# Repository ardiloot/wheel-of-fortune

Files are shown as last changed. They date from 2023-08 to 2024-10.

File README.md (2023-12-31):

# Wheel of Fortune

## Overview

An over-engineered DIY version of Wheel of Fortune (Wheel or Prizes). The main features are:
* 3 LED strips with individually controllable LEDs (WLED)
* 3 linear servo motors for displaying effect logos
* absolute position optical encoder for wheel position (position depended effects)
* Amplified sound system for theme and effect sound
* ESP32 based LED and servo motor controller
* Orange PI 3 LTS based compute unit
* Node (React + Mantine) app for configuration
* Server stack for metrics, monitoring and backup

Outlook:

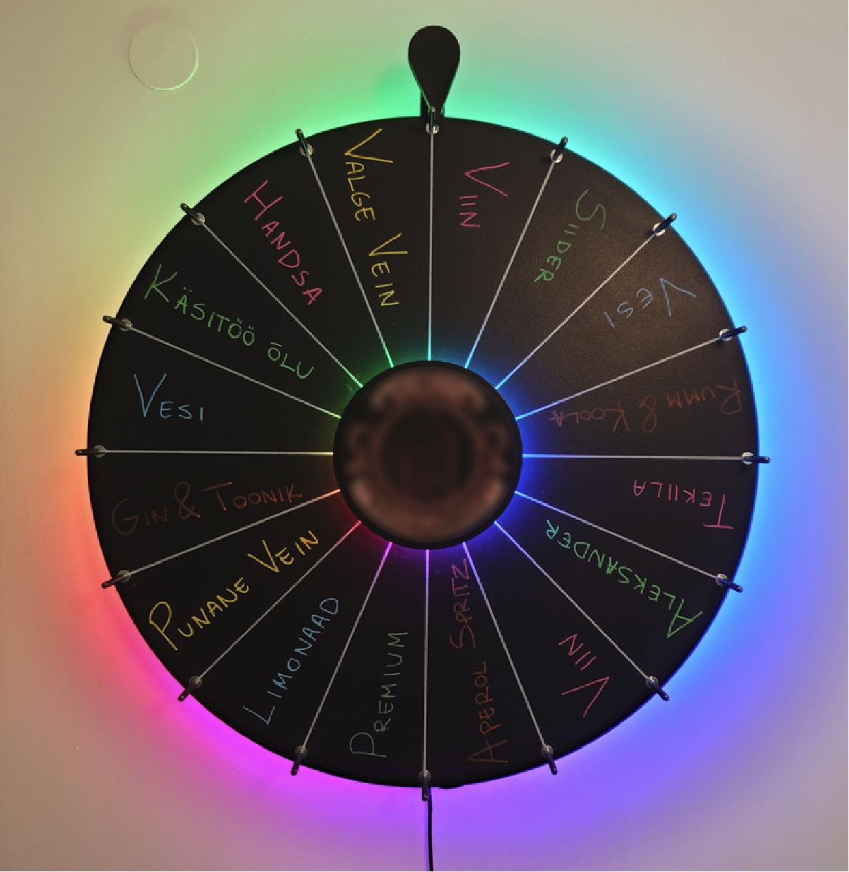
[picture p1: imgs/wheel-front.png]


Internals:

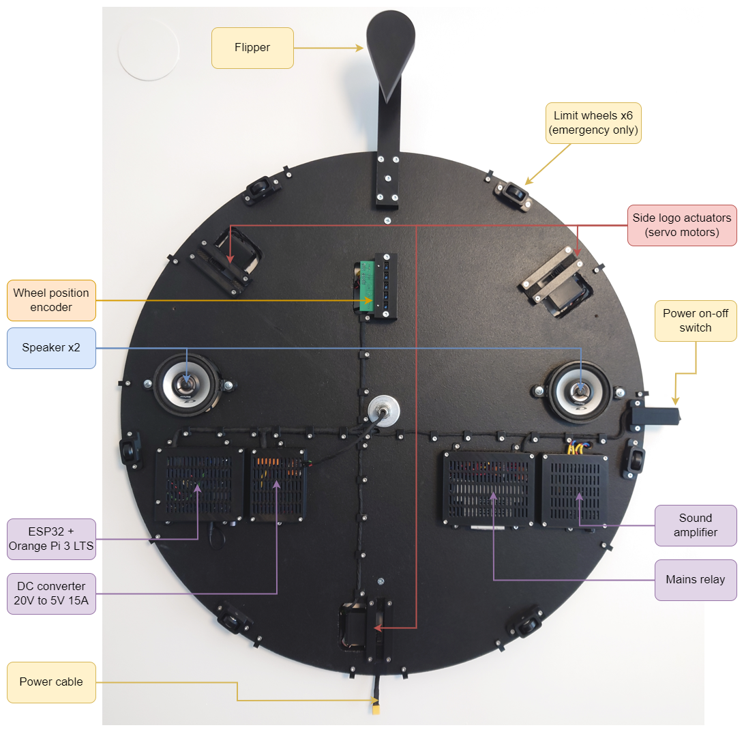
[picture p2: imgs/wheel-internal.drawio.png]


Services:

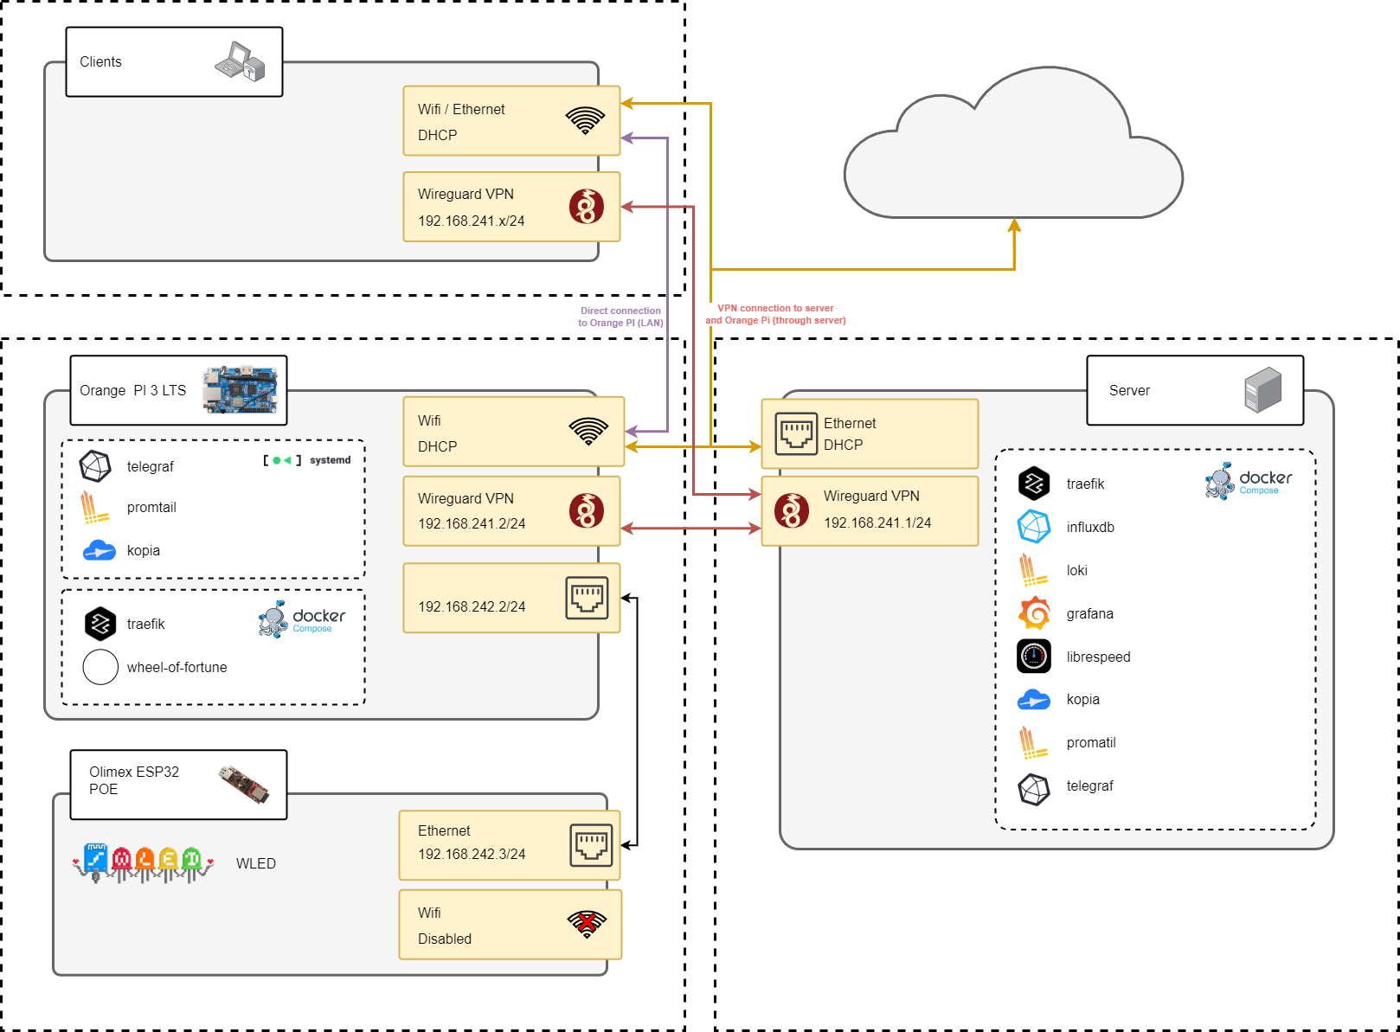
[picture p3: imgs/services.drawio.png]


For detailed instructions how to build the system, see following readme files:

1. [Mechanical setup](hw/mech)
1. [Electrical setup](hw/electrical)
1. [Embedded software](embedded_software)
1. [Server software](server)

## Development

Code is split to two main parts:
1. [Python backend](wheel_of_fortune) (FastAPI)
1. [Node frontend](wheel_of_fortune/frontend) (React + Mantine)

Finally, frontend static HTML + Javascript files are backed into backend Python package and served via backend FastAPI server. 

### Backend

#### Development environment

Python 3.11 is currently preferred, but should also work on any Python >= 3.10

```bash
python -m venv venv
source venv/bin/activate
pip install -r dev-requirements.txt
pip install -e .
```

#### Running backend

```bash
source venv/bin/activate
python -m wheel_of_fortune
```

#### Updating requirements

After adding dependency update requirement files by running:

```bash
source venv/bin/activate
pip-compile --upgrade -o requirements.txt pyproject.toml \
    && pip-compile --extra dev --upgrade -o dev-requirements.txt pyproject.toml \
    && pip-sync dev-requirements.txt
```

### Frontend

#### Setup development environment

Install `nvm` and `node` and install dependencies:

```bash
cd wheel_of_fortune/frontend/
curl -o- https://raw.githubusercontent.com/nvm-sh/nvm/v0.39.4/install.sh | bash
source ~/.bashrc
nvm install
nvm use
npm ci
```

#### Developer mode

Create `.env.local` file for overriding environment:

```bash
VITE_API_URL=https://wheel.int.example.com/api/v1
VITE_WS_URL=wss://wheel.int.example.com/api/v1/ws
```

Run frontend in `dev` mode:

```bash
nvm use
npm run dev
```

#### Release build

```bash
nvm use
npm run build
```

#### Update packages

To update `package-lock.json` and install updates:

```bash
npm update
npm install
```

To also update `package.json` file:

```bash
npm install -g npm-check-updates
ncu -u
npm install
```

### Build steps

Usually not needed, as [Github actions](tree/main/.github/workflows) automatically build and test frontend & docker images. But for completeness, here are commands to do build manually:

#### Frontend

```bash
cd wheel_of_fortune/frontend/
nvm use
npm ci
npm run build
cd ../..
```

#### Backend

```bash
python -m build
```

#### Docker image

```bash
docker build -t wheel_of_fortune .
```

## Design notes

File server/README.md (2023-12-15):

# (Metrics) server setup

## Overview

The aim of this server is to collect logs & telemetry and provide VPN network for Wheel of Fortune:

1.  Server for logs (Loki)
2.  Server for storing telemetry (Influx)
3.  Dashboards for logs and telemetry (Grafana)
4.  VPN network for remote access (WireGuard)
5.  Backup repository (Kopia)

Following services are exposed through Traefik reverse proxy:

- https://traefik.int.example.com - Traefik internal dashboard (basic HTTP auth)
- https://influxdb.int.example.com - Influxdb admin panel
- https://loki.int.example.com - Loki API
- https://grafana.int.example.com - Grafana dashboards
- https://librespeed.int.example.com - Speedtest for testing connection
- https://int.example.com:51515 - Kopia

Throughout this document, `example.com` is use as a example domain name. All services are accessible only over VPN.

## Setup compute instance

One option is to use Oracle Cloud free instance:

- Instance name: wheelmetrics
- Shape: ARM Ampere A1 (VM.Standard.A1.Flex), 1 OCPU, 6 GB RAM
- Image: Canonical Ubuntu 22.04 Minimal aarch64
- Networking: public IPv4 address
- SSH keys: add your public SSH key
- Boot volume: 47 GB

Could use any other cloud provider or local compute.

## Setup domain name

Setup DNS A-type records to point your domain name (`example.com`) to public IP (`a.b.c.d`) of the instance:

```
a.b.c.d     A       example.com
a.b.c.d     A       *.example.com
```

## Setup firewall

Follow steps: https://www.digitalocean.com/community/tutorials/how-to-set-up-a-firewall-with-ufw-on-ubuntu-22-04

## Setup VPN

Follow steps from [Digital Ocean](https://www.digitalocean.com/community/tutorials/how-to-set-up-wireguard-on-ubuntu-22-04) tutorial.

Remember to allow WireGuard port (`51820/udp`) through firewall(s) and allow traffic from developer VPN clients to Wheel of Fortune for remote access:

```bash
sudo ufw allow 51820/udp
sudo ufw route allow in on wg0 out on wg0 to 192.168.241.2
```

As an example, WireGuard could use subnet `192.168.241.0/24`:

1. `192.168.241.1` - current server
2. `192.168.241.2` - Wheel of Fortune (OrangePi)
3. `192.168.241.3` - developer access #1
4. `192.168.241.4` - developer access #2
5. ...

Add DNS records for the server (`int.example.com`) and for Wheel of Fortune VPN ip-address (`wheel.int.example.com`):

```dns
int.example.com             A   192.168.241.1
*.int.example.com           A   192.168.241.1
wheel.int.example.com       A   192.168.241.2
*.wheel.int.example.com     A   192.168.241.2
```

Subdomain `*.int.example.com` correspond to resources accessible over VPN (everything in this case).

## Install docker engine:

Follow steps in: [Installing docker on Ubuntu](https://docs.docker.com/engine/install/ubuntu)

Redirect logging to `journald` for easier scaping by promtail. Create file

```bash
sudo nano /etc/docker/daemon.json
```

with contents

```json
{
   "log-driver": "journald"
}
```

## Setup metrics stack

Clone repository:

```bash
cd ~
git clone https://github.com/ardiloot/wheel-of-fortune.git
```

Copy environment file from the example and fill in values :

```bash
cd ~/wheel-of-fortune/server/metrics
cp env.example .env
nano .env
```

PS: `TELEGRAF_INFLUXDB_*` variables can be filled in later

Start metrics stack:

```bash
docker compose up -d
```

If getting permission errors from Grafana or Loki, run to fix permissions:

```bash
sudo chown 10001:10001  ~/data/loki/
sudo chown 472:472  ~/data/grafana/
```

## Configure influxdb

https://influxdb.int.example.com/

Initial setup:

- Username: admin
- Organization: wheelmetrics
- Bucket name: telegraf

API token for telegraf: (Generate API token -> Custom API token)

- Description: Server's telegraf write token
- Permissions: Add write permissions to telegraf bucket

Create bucket for Wheel of Fortune telemetry: (Buckets -> Create bucket)

- Name: wheel-of-fortune

API token for Wheel of Fortune: (Generate API token -> Custom API token)

- Description: Wheel of Fortune write token
- Permissions: Add write permissions to wheel-of-fortune bucket

Create bucket for Traefik telemetry: (Buckets -> Create bucket)

- Name: traefik

API token for Traefik: (Generate API token -> Custom API token)

- Description: Traefik write token
- Permissions: Add write permissions to traefik bucket

API token for Grafana: (Generate API token -> Custom API token)

- Description: Grafana read all token
- Permissions: Read all buckets

Add generated telegraf token to `.env` file (`TELEGRAF_INFLUXDB_TOKEN`) and restart docker stack `docker compose up -d`.

## Configure Grafana

https://grafana.int.example.com

Default user/password: admin/admin

Add telegraf data source: Administration -> Data sources -> Add data source -> InfluxDB:

- Name: Telegraf
- Query language: InfluxQL
- URL: http://influxdb:8086
- Custom HTTP Headers, select Add Header. Set header to `Authorization` and value to `Token [token]` (previously generated read Token for Grafana)
- Database: telegraf

Add Wheel of Fortune data source: Administration -> Data sources -> Add data source -> InfluxDB:

- Name: Wheel of Fortune
- Query language: InfluxQL
- URL: http://influxdb:8086
- Custom HTTP Headers, select Add Header. Set header to `Authorization` and value to `Token [token]` (previously generated read Token for Grafana)
- Database: wheel-of-fortune

Add Traefik data source: Administration -> Data sources -> Add data source -> InfluxDB:

- Name: Traefik
- Query language: InfluxQL
- URL: http://influxdb:8086
- Custom HTTP Headers, select Add Header. Set header to `Authorization` and value to `Token [token]` (previously generated read Token for Grafana)
- Database: traefik

Add dashboards for Telegraf metrics. For example: https://grafana.com/grafana/dashboards/928-telegraf-system-dashboard/

Add Loki data source: Administration -> Data sources -> Add data source -> Loki:

- Name: Loki
- URL: http://loki:3100

## Configure kopia

For the first start, add `--tls-generate-cert` option to the command to automatically generate TLS certs.

Create repository:

```bash
docker exec -it kopia kopia repository create filesystem --path=/repository
```

Add user for Wheel of Fortune:

```bash
docker exec -it kopia kopia server user add root@wheel-of-fortune
```

Dashboard is located at https://int.example.com:51515

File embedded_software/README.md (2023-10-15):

# Embedded software

## Orange Pi 3 LTS setup

### Burn image to SD card

Follow steps outlined in User Manual (chapters 2.4 - 2.5) to burn Ubuntu server image (`Orangepi3-lts_3.0.8_ubuntu_jammy_server_linux5.16.17.7z`) to SD card.

[Manual and downloads](http://www.orangepi.org/html/hardWare/computerAndMicrocontrollers/service-and-support/Orange-pi-3-LTS.html)

### Initial configuration

Install SD card and power on the Orange Pi board.
To complete initial config, monitor and keyboard must be connected (or Ethernet cable for SSH access). Login using default username & password: orangepi/orangepi

1. Change user password (`passwd`)
2. Connect to WiFi (User Manual chapter 3.8.2)

```bash
nmcli dev wifi
nmcli dev wifi connect [wifi_name] password [wifi_passwd]
```

3. Install updates

```bash
sudo apt-get update
sudo apt-get upgrade
```

4. Add your public SSH key to `~/.ssh/authorized_keys`
5. Disable password login (`sudo nano /etc/ssh/sshd_config`, edit relevant line to `PasswordAuthentication no`)
6. Reboot (`sudo reboot`)

This concludes initial configuration, rest of the configuration can be done over SSH.

### Install WiringOP

Install utilities for controlling GPIO. For more information see User Manual chapter "3.18 How to install wiringOP".

```bash
git clone https://github.com/orangepi-xunlong/wiringOP
cd wiringOP
sudo ./build clean
sudo ./build
```

Test GPIO (should see a table with GPIO current status):

```bash
gpio readall
```

### Set static IP to Ethernet interface

Ethernet port is used to connect to Olimex ESP32 POE running WLED software.
WLED and Ethernet interface should have IP addresses from the same subnet.
In this example, WLED is configured to have static IP `192.168.242.3/24`
and Orange PI's Ethernet port to `192.168.242.2/24`.

```bash
nmcli con mod "Wired connection 1" ipv4.addresses "192.168.242.2/24" ipv4.method "manual"
```

Reboot the system for changes to take effect.

### GPIO permissions

Modify udev rules to allow acces of non-root users to GPIO. Create file

```bash
sudo nano /etc/udev/rules.d/99-gpio.rules
```

with following contents:

```bash
SUBSYSTEM=="gpio", KERNEL=="gpiochip*", ACTION=="add", PROGRAM="/bin/sh -c 'chown root:orangepi /sys/class/gpio/export /sys/class/gpio/unexport ; chmod 220 /sys/class/gpio/export /sys/class/gpio/unexport'"
SUBSYSTEM=="gpio", KERNEL=="gpio*", ACTION=="add", PROGRAM="/bin/sh -c 'chown root:orangepi /sys%p/active_low /sys%p/direction /sys%p/edge /sys%p/value ; chmod 660 /sys%p/active_low /sys%p/direction /sys%p/edge /sys%p/value'"
```

Reboot the system for changes to take effect.

### Install Docker

Install Docker following the instructions from the Docker's home page:
[instructions](https://docs.docker.com/engine/install/ubuntu/#install-using-the-repository).

Also complete [linux postinstall](https://docs.docker.com/engine/install/linux-postinstall/) steps.

By default Docker logs to disk and causes SD card wear.
To avoid that, redirect logging to `journald`. Create file

```bash
sudo nano /etc/docker/daemon.json
```

with contents

```json
{
   "log-driver": "journald"
}
```

## GPIO poweroff service

This service listens GPIO port for shutdown signal (physical poweroff switch).
Only use this service, if poweroff switch is installed. 
For installation, follow instructions from [gpio_poweroff/README.md](gpio_poweroff/README.md).

## Setup VPN (optional)

Follow instructions starting from:
[here] (https://www.digitalocean.com/community/tutorials/how-to-set-up-wireguard-on-ubuntu-22-04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)

Use following configuration:

```bash
sudo nano /etc/wireguard/wg0.conf
```

```
[Interface]
Address = 192.168.241.2
PrivateKey = !REPLACE!

[Peer]
PublicKey = !REPLACE!
Endpoint = example.com:51820
AllowedIPs = 192.168.241.0/24
PersistentKeepalive = 25
```

Configure VPN to always restart:

`sudo systemctl edit wg-quick@wg0.service`

```
[Unit]
StartLimitIntervalSec=0
After=network-online.target
Wants=network-online.target

[Service]
Type=simple
Restart=always
RestartSec=5s
```

## Setup telegraf (optional)

https://docs.influxdata.com/telegraf/v1.21/introduction/getting-started/

1. Install `sudo apt-get install lm-sensors`
1. Enable `outputs.influxdb_v2`
2. Enable `inputs.sensors`

## Setup promtail (optional)

To send logs to Loki, configure promtail to scrape journald.

First, install promtail:

```bash
wget https://github.com/grafana/loki/releases/download/v2.8.4/promtail-linux-arm64.zip
unzip promtail-linux-arm64.zip
rm promtail-linux-arm64.zip
sudo mv promtail-linux-amd64 /usr/local/bin/promtail
# Verify
promtail --version
```

Create configuration file

```bash
sudo mkdir -p /etc/promtail
sudo mkdir -p /var/lib/promtail/
sudo nano /etc/promtail/config.yaml
```

with contents (replace server and auth info).

```yaml
server:
  disable: true

positions:
  filename: /var/lib/promtail/positions.yaml

clients:
  - url: https://[replace]/loki/api/v1/push
    basic_auth:
      username: [replace]
      password: [replace]

scrape_configs:
  - job_name: journal
    journal:
      max_age: 12h
      json: false
      labels:
        job: systemd-journal
    # see https://www.freedesktop.org/software/systemd/man/systemd.journal-fields.html#Trusted%20Journal%20Fields
    # see https://grafana.com/docs/loki/latest/clients/promtail/scraping/#journal-scraping-linux-only
    # NB use `journalctl -n 1 -o json | jq .` to see an actual journal log message (including metadata).
    # NB use `journalctl -n 1 -o json CONTAINER_NAME=date-ticker | jq .` to see a container log message.
    relabel_configs:
      - source_labels: [__journal__hostname]
        target_label: host
      - source_labels: [__journal__systemd_unit]
        target_label: source
      - source_labels: [__journal_container_name]
        target_label: container_name
      - source_labels: [__journal_image_name]
        target_label: image_name
      - source_labels: [__journal_workflow_id]
        target_label: workflow_id
      - source_labels: [__journal__boot_id]
        target_label: boot
      - source_labels: [__journal_priority]
        target_label: priority
    pipeline_stages:
      - template:
          source: priority
          template: '{{ if eq .Value "0" }}{{ Replace .Value "0" "emerg" 1 }}{{ else if eq .Value "1" }}{{ Replace .Value "1" "alert" 1 }}{{ else if eq .Value "2" }}{{ Replace .Value "2" "crit" 1 }}{{ else if eq .Value "3" }}{{ Replace .Value "3" "err" 1 }}{{ else if eq .Value "4" }}{{ Replace .Value "4" "warning" 1 }}{{ else if eq .Value "5" }}{{ Replace .Value "5" "notice" 1 }}{{ else if eq .Value "6" }}{{ Replace .Value "6" "info" 1 }}{{ else if eq .Value "7" }}{{ Replace .Value "7" "debug" 1 }}{{ end }}'
      - labels:
          priority:
```

To start promtail automatically, create a systemd service

```
sudo nano /etc/systemd/system/promtail.service
```

with content:

```
[Unit] 
Description=Promtail service 
After=network-online.target
Wants=network-online.target 

[Service] 
Type=simple 
User=root 
ExecStart=/usr/local/bin/promtail -config.expand-env=true -config.file /etc/promtail/config.yaml 
Restart=on-failure 
RestartSec=20 
 
[Install] 
WantedBy=multi-user.target
```

To enable and test the service, run:

```bash
sudo systemctl daemon-reload
sudo systemctl enable promtail
sudo systemctl start promtail
sudo systemctl status promtail
```

### Setup Kopia (optional)

Install Kopia by following steps from [their webpage](https://kopia.io/docs/installation/#linux-installation-using-apt-debian-ubuntu):

```bash
curl -s https://kopia.io/signing-key | sudo gpg --dearmor -o /etc/apt/keyrings/kopia-keyring.gpg
echo "deb [signed-by=/etc/apt/keyrings/kopia-keyring.gpg] http://packages.kopia.io/apt/ stable main" | sudo tee /etc/apt/sources.list.d/kopia.list
sudo apt update
sudo apt install kopia
```

Setup Kopia to backup to remote repository ([docs](https://kopia.io/docs/repository-server/#on-client-computer)):

```bash
sudo su
kopia repository connect server --url https://int.example.com:51515 --server-cert-fingerprint=[REPLACE]
kopia snapshot create /home/orangepi/data
```

Create service to make daily backups:

`/etc/systemd/system/kopia.service:`

```
[Unit]
Description=Kopia backup
Wants=network-online.target
After=network-online.target

[Service]
Type=oneshot
PrivateTmp=true
Environment="HOME=/root"
ExecStart=/usr/bin/kopia snapshot create --all
```

`/etc/systemd/system/kopia.timer:`

```
[Unit]
Description=Run kopia backup

[Timer]
OnCalendar=daily
Persistent=true
Unit=kopia.service

[Install]
WantedBy=timers.target
```

To enable the service, run:

```bash
sudo systemctl daemon-reload
sudo systemctl enable kopia
sudo systemctl start kopia
sudo systemctl status kopia
```

### Python (optional)

If used for development, install `venv` and `python3-dev`:

```bash
sudo apt-get install python3.10-venv python3-dev
```

## WLED

```bash
git subtree pull --prefix embedded_software/WLED https://github.com/Aircoookie/WLED.git v0.14.0-b4 --squash
```

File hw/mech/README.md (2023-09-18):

# Mechanical design

This file contains documentation for the mechanical design. It is structured as a step-by-step guide to fabricate all necessary components and assemble them together.

NB: Not all details are included in this guide, please consult with the [bill of materials (BOM)](../bom/bom.pdf) and 3D models for complete information.

## 3D printed parts

* Printer: Ender-3 V2 (Trianglelab DDB Extruder V2.0 + BLTouch)
* Slicer: Ultimaker Cura 4.11.0

Rigid parts (PLA+):

* Filamant: eSun PLA+ 1.75mm 1kg Black
* Profile: Standard Quality
* Printing temperature: 210 °C
* Build Plate Temperature: 60 °C
* Initial layer horizontal expansion: -0.1 mm
* Generate support: yes (if needed)

Flexible parts (TPU):

* Filament: Overture TPU Filament, 1.75 mm, black
* Profile: Standard Quality
* Printing temperature: 210 °C
* Build Plate Temperature: 60 °C
* Print speed: 10 mm/s
* Enable retraction: False
* Initial layer horizontal expansion: -0.1 mm

## Wheel assembly

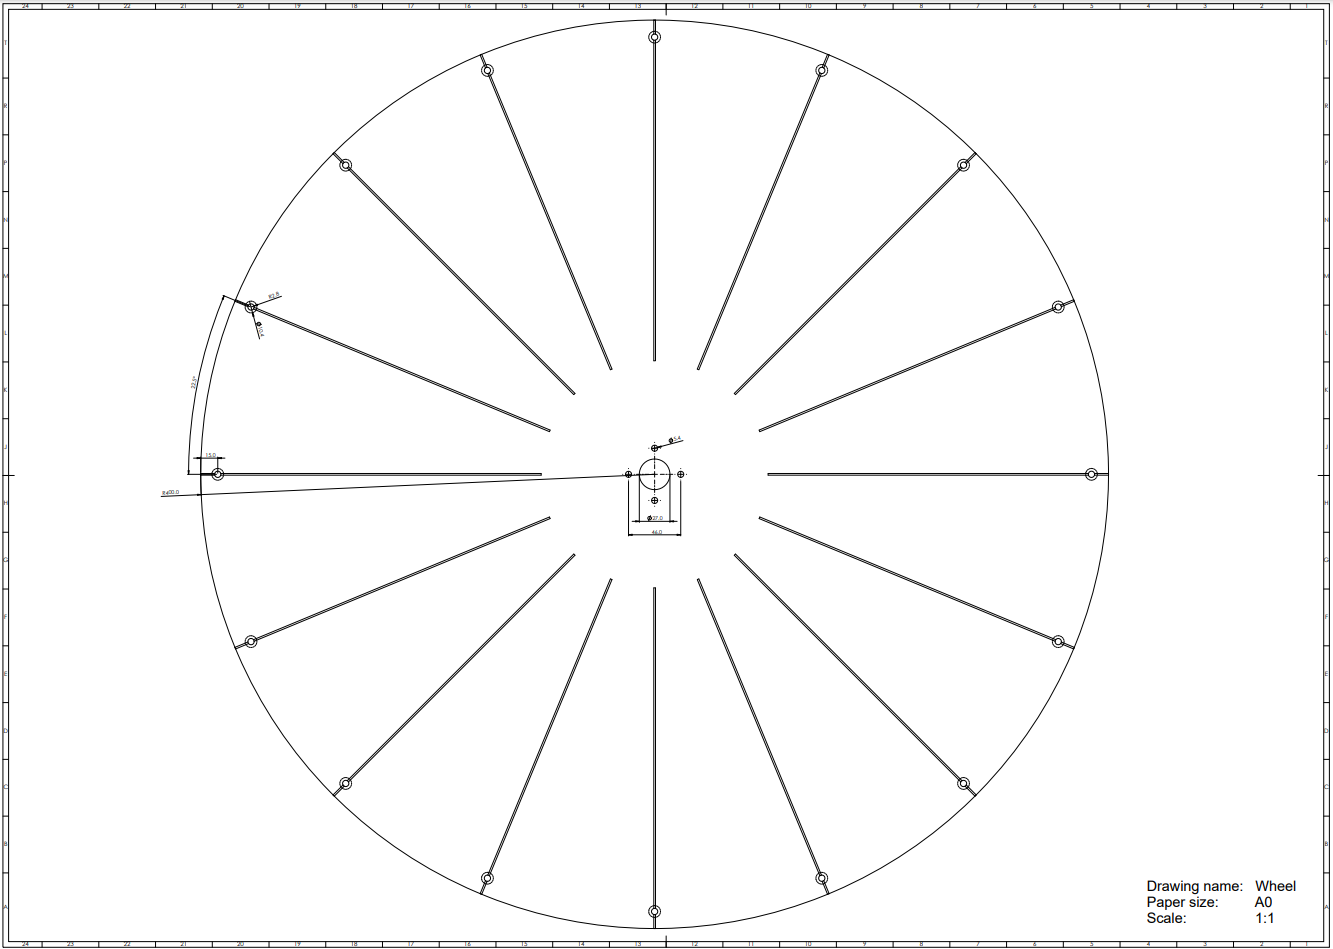
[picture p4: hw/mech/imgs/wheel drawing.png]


[Drawing PDF](wheel/wheel%20drawing.pdf)

[Assembly 3D model](wheel/wheel%20assembly.STL)

### Cut out the wheel

Use drawing to cut out a circle (wheel) from 18 mm thick plywood / particle board. Do not drill any holes yes, before attaching encoder pattern (next step).

### Paint the wheel

Finish the wheel with blackboard paint on the one side and optionally also paint the back side of the wheel (any color). Use appropriate color edge banding to finish the edge.

### Print and glue encoder pattern 

Print [encoder pattern](wheel/encoder_pattern/pattern.pdf) to `A2` sized paper and cut the excess paper outside the pattern (less paper to glue). Use spray glue (or similar) to glue the patter exactly to the center of the wheel.

### Drill holes

Now rest of the holes can be drilled by following the markings on the encoder pattern (center hole, 4 mounting holes and 16 holes for sector separators). To accurately drill the holes for the sector separation rods, it is possible to use following 3D printed [drill aid](wheel/drill%20aid.STL) (needs `605zz 5x14x5mm` bearings or similar, 5 pcs)

### Draw sector separation lines

Use waterproof permanent marker to draw lines between sectors.

### Attach sector separation rods

Attach rods between sectors. Consult [BOM](../bom/bom.pdf) for details.

### Bearing hub

First, print extension to the bearing hub [STL](wheel/bearing%20hub%20ext.STL) as of the shelf bearing hub is not meant to have two bearings inside the hub side-by-side.

Secondly, drill 4 holes into a large washer (`DIN125 M33`) for M5 countersunk heads. Use [drill aid](wheel/drill%20aid%202.STL) (needs `605zz 5x14x5mm` bearings or similar, 4 pcs)

Finally, insert two `SKF6201` (or similar) bearings into the bearing hub and attach them to the wheel by 4 screws (details in [BOM](../bom/bom.pdf)).

### Finishing up

Last step of the wheel assembly is to write names to different sectors to your liking. Liquid chalk markers can be used.

## Backplate assembly

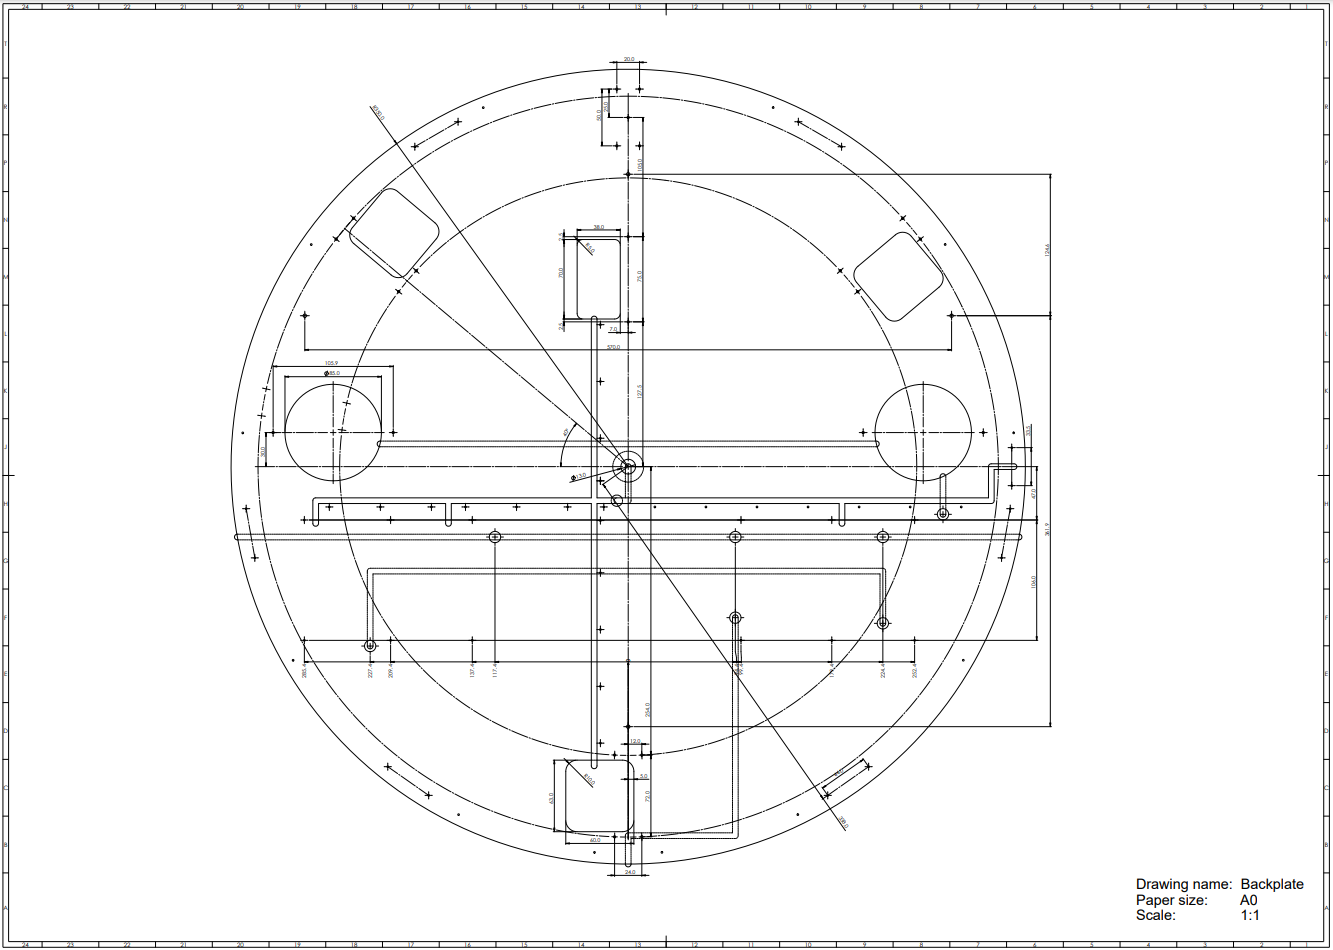
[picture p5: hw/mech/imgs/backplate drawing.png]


[Drawing PDF](backplate/backplate%20drawing.pdf)

[Assembly 3D model](backplate/backplate%20assembly.STL)

### Cut out backplate

Use 18 mm thick plywood / particle board to cut out a circle with 700 mm diameter. As backplate has many holes for mounting sub-assemblies and for passing wires it is advised to print out [drawing](backplate/backplate%20drawing.pdf) to `A0` sized paper and use it as a stencil. This is probably the easiest way to accurately drill/saw all the necessary holes. Also, the stencil can be used in assembly phase to mount all the sub-assemblies correctly.

NB: all/most smaller holes do not need to be drilled, as they are just position markers for wood screws.

### Linear actuator sub-assembly

### Limit wheel sub-assembly

There are 6 limit wheels for stopping the wheel if it is bent by using considerable about of force. In other words, they are only for limiting the movement of the wheel in extreme cases to avoid damaging other components between the wheel and the backplate.

It uses 3D printer pulley wheels and custom 3D printed mount. Consult [BOM](../bom/bom.pdf) for details.

[3D printed parts](backplate/limit%20wheel/limit%20wheel%20assembly.STL)

[Assembly 3D model](backplate/limit%20wheel/limit%20wheel%20assembly.STL)

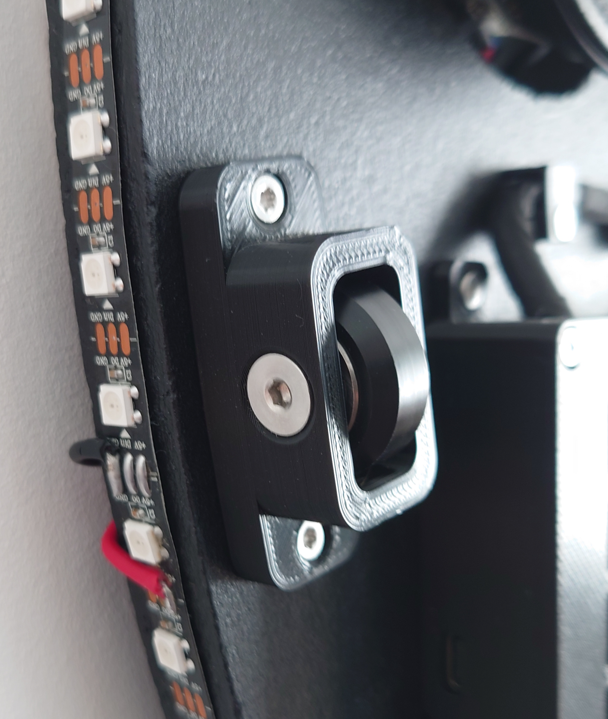
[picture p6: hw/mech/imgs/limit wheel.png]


### Encoder sub-assembly

Encoder sub-assembly if for attaching encoder PCB to the backplate.

[3D printed parts](backplate/encoder)

[Assembly 3D model](backplate/encoder/encoder%20assembly.STL)

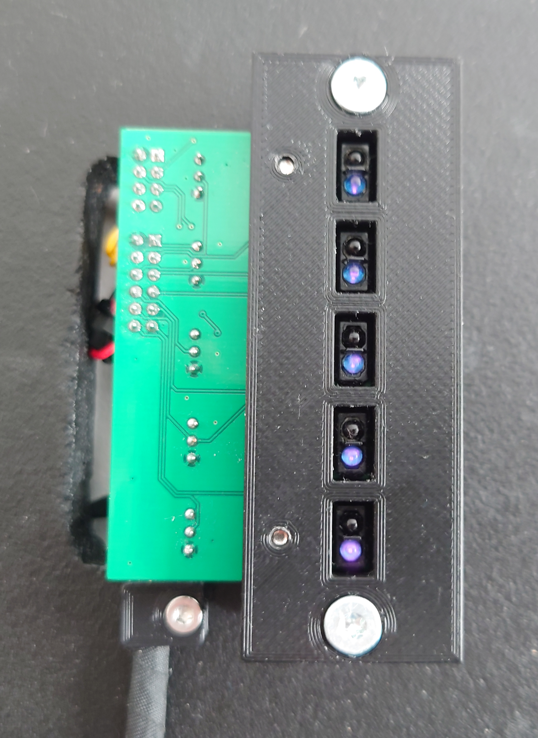
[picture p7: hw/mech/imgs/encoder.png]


### Compute sub-assembly

Compute sub-assembly holds Orange Pi 3 LTS and Olimex ESP32 POE boards. 

[3D printed parts](backplate/compute)

[Assembly 3D model](backplate/compute/compute%20assembly.STL)

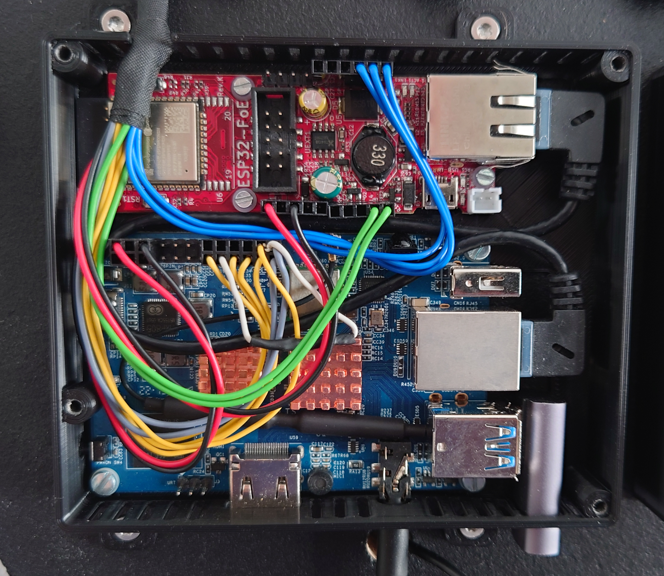
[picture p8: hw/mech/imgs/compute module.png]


### DC converter sub-assembly

DC converter module is for mounting the main DC voltage converter (20 to 5 V). Works as a main power distribution box, as almost everything is powered by 5 V.

[3D printed parts](backplate/dc%20converter)

[Assembly 3D model](backplate/dc%20converter/dc%20converter%20assembly.STL)

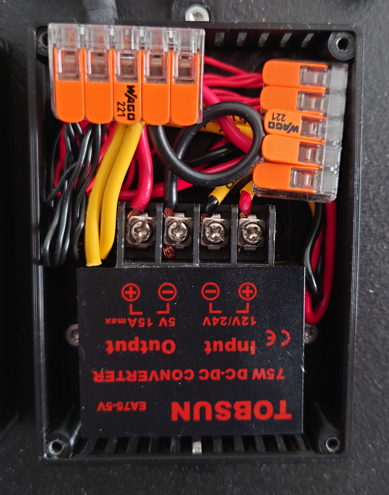
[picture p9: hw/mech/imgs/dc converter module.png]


### Power relay sub-assembly

Power relay module is the main distribution box for 20 V and it also is responsible for switching off the wheel electronics with delay to allow graceful shutdown of the Orange PI board.

[3D printed parts](backplate/power%20relay)

[Assembly 3D model](backplate/power%20relay/power%20relay%20assembly.STL)

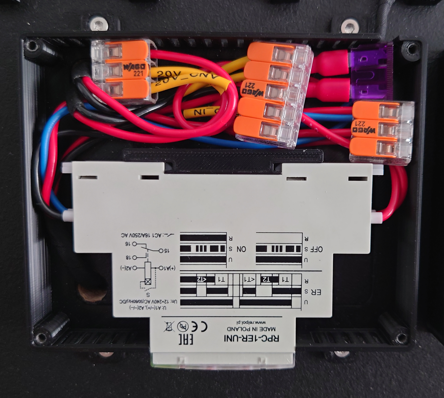
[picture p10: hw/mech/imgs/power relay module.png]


### Amplifier sub-assembly

Mounts sound amplifer and ground loop isolator.

[3D printed parts](backplate/amplifier/)

[Assembly 3D model](backplate/amplifier/amplifier%20assembly.STL)

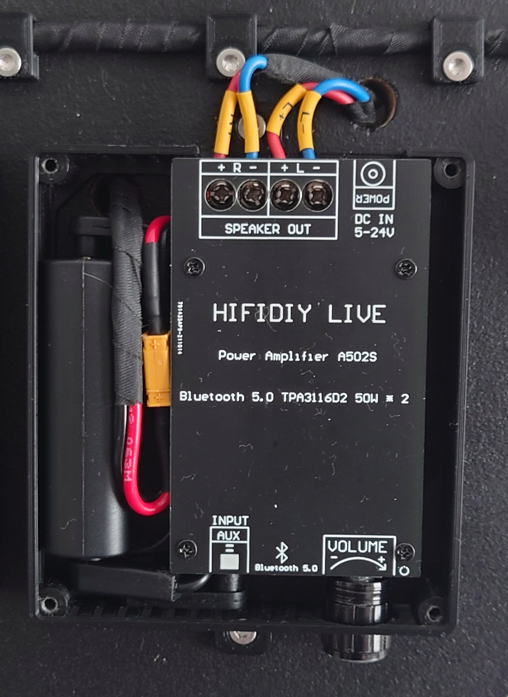
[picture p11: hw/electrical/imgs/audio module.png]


### Flipper sub-assembly

### Power switch sub-assembly

### Speakers

## Cover logo assembly

[Assembly 3D model](cover/cover%20assembly.STL)

## Final assembly

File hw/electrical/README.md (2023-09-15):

# Electrical design

[Wiring diagram](wiring%20diagram.pdf) of the Wheel of Fortune shows how to wire together different modules of the system (displayed as rectangles with round edges). It tries to follow the physical layout of the components if possible. Different wiring colors show different purpose of the wires and are described in the legend. All connectors are displayed from the "top view" (wires going into the screen).

In the following chapters each submodule is separately described together with its connections.

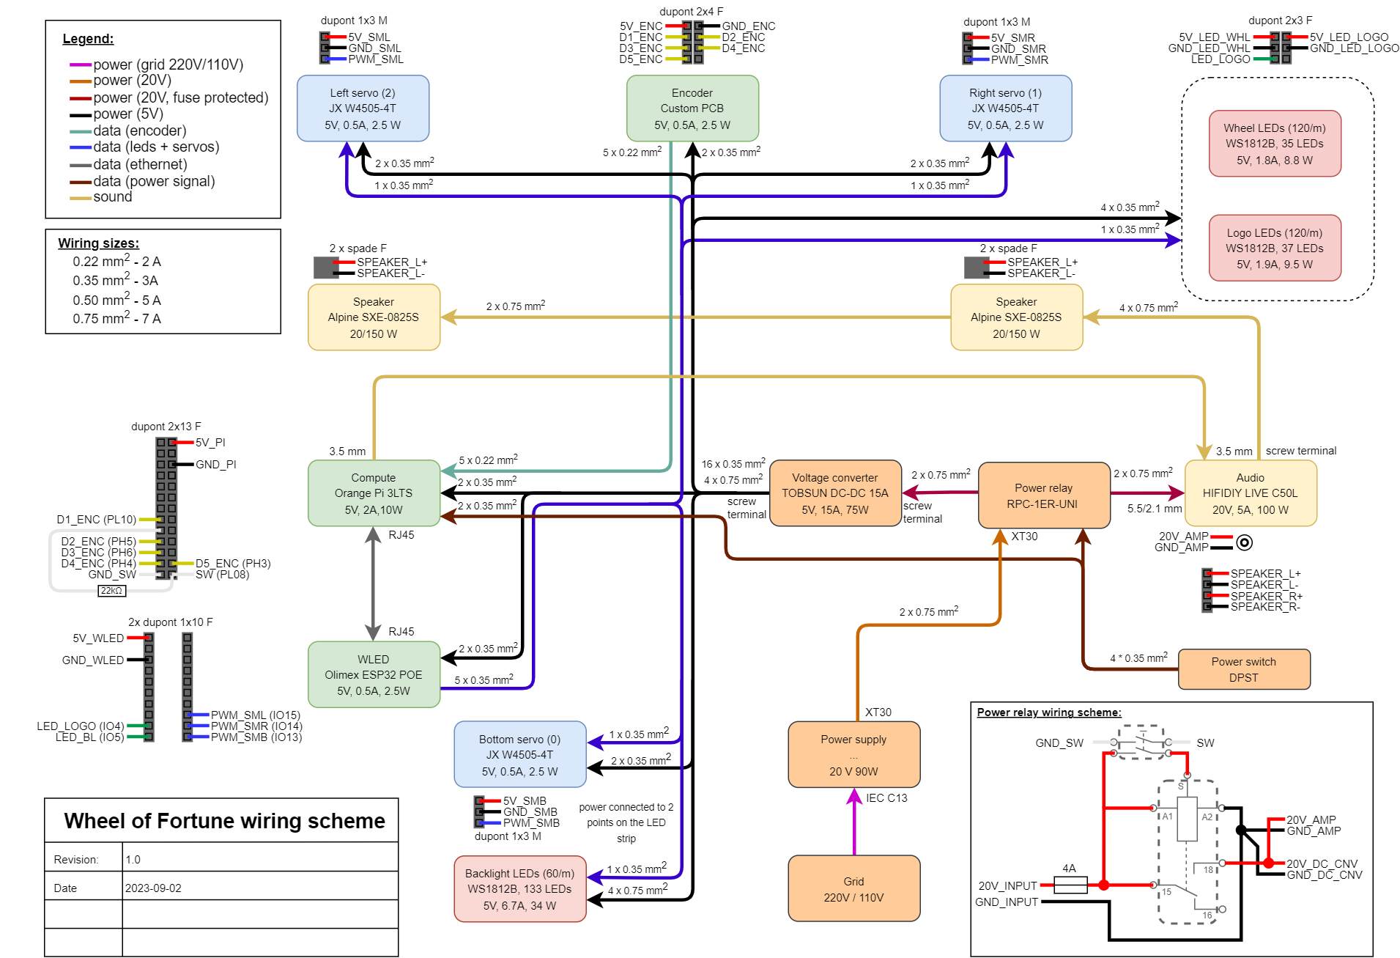
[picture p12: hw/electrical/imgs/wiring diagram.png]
Wiring diagram


## Backlight LEDs

A long led strip attached to the side of the backplate.

As LED strip can draw considerable amount of current (6.7 A), it is advised to power the LED strip form two distinct points (e.g. 1/4 and 3/4). Thick wires should be used (0.75 mm<sup>2</sup>). It is easiest to just solder power wires to the LED strip, but use of connectors is also possible if needed.

Power wires lead to `voltage converter` module and data wire is connected to `WLED` module (ESP32).

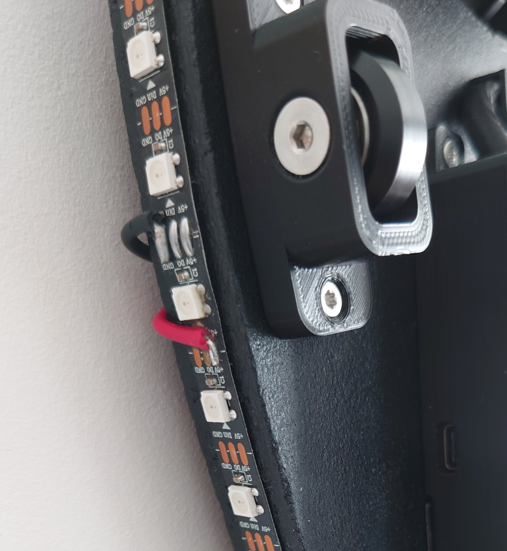
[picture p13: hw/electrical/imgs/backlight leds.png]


## Logo and wheel LEDs

Inside the center logo assembly there are two additional LED strips. Logo LED strip is used as a backlight to the logo and wheel LED strip is illuminating the front of the wheel.

They are powered separately from `voltage converter` module, but they share the data wire (like we have one long LED strip).

## Servo motors

Wheel of Fortune has 3 servo motors (`JX W4505-4T`) used to display side logos. They are regular 5V servos capable of doing multiple turns (to have enough actuation range). They are powered from `voltage converter` module and controlled by `WLED` module (ESP32).

3-pin Dupont connector is used to connect the motor.

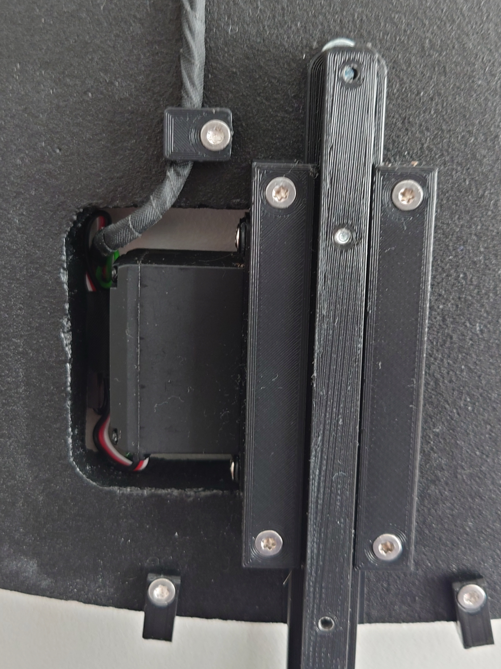
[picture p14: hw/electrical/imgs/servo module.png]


## Encoder

Encoder module contains of 5 line sensors that is used to monitor the encoder pattern attached to the back side of the wheel plate. One sensor is used for clock (and speed) signal and the rest of 4 sensors are used to have absolute positioning of the wheel (2<sup>4</sup> = 16 sectors). Accurate position inside of the sector is not monitored.

Encoder module is powered form `voltage converter` module (5 V) and the position of the wheel is communicated through 5 digital outputs (3.3 V) to `compute` module (Orange Pi).

Details of the schematic and manufacturing of the module can be found in [README](line_sensor_encoder/README.md) file.

Audio module

## Power switch

Power switch is used (`DPST MRS201-3C3`) is used to gracefully power off and on the the electronics. Double Pole Single Throw (DPST) switch is used to send information to the `compute` module (Orange Pi) and to `power relay` module. If power is switched off, the `compute` module can initiate clean shutdown and `power relay` module can start countdown to cut the power (e.g. 30 secs). It should avoid disk corruption of the `compute` module.

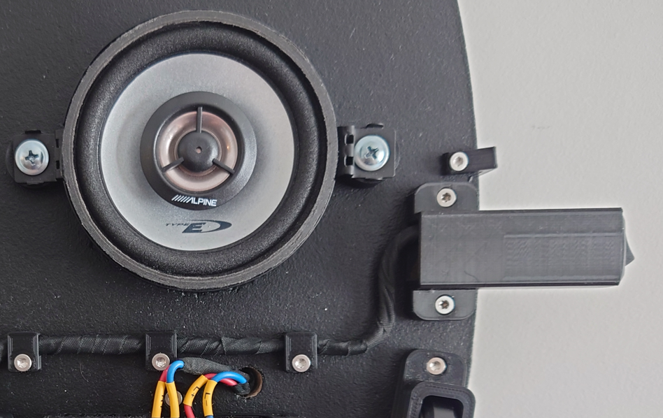
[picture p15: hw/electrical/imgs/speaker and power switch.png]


## Speakers

System has two speakers (`Alpine SXE-0825S`, RMS power 20W, peak power 150W). They are connected with spade connectors to the `audio` module.

## Audio module

Audio module mainly consists of:
1. Audio amplifier (`A502S TPA3116D2 50W`)
2. Ground loop isolator (`Kebidumei`)

Ground loop isolator is needed to avoid noise from the ground loop as Orange Pi (source of audio) and sound amplifier are are sharing ground connection. Adding sound cable is creating a ground loop unless isolator is used.

Module is powered from `power relay` module (20 V). On the image a custom power connector (`XT30`) is used, however standard barrel connector can also be used. Audio signal originates from `compute` module (Orange Pi).



## Compute module

Compute module contains two sub-modules:
1. Orange Pi 3 LTS compute board
2. Olimex ESP32 POE

Orange Pi is the main compute unit of the system. It is powered from 5V and it has encoder module connected to its GPIO pins. Also, it is connected to the power switch to for shutdown signal. Note, that poweroff pin needs pull-up resistor.

ESP32 unit runs modified WLED software and is responsible for controlling LED strips and servo motors. It is powered by 5V and it has 3 PWM outputs for servo motors and 2 outputs for controlling LED strips. For ESP32 pinout see [here](olimex%20esp32%20pinout.pdf).

Two units are connected together with short Ethernet cable.



## Voltage converter

Almost all electronics are running on 5 V and this module is responsible for providing enough 5 V power. As LED strips can be power hungry (full brightness at white color) then this power module must be rated to 15 A (realistic max usage around 12 A).

Here, to keep it simple, a low cost 5 V converter (`TOBSUN 12V/24V TO 5V 15A`) is used together with two `WAGO 221-415` connectors. Module is powered from `power relay` module (20V) and 5 V power is distributed to almost all other module in the system.

NB: Wires from the converter to the WAGO connectors must be rated for 15 A (cross section > 1.5 mm<sup>2</sup>)

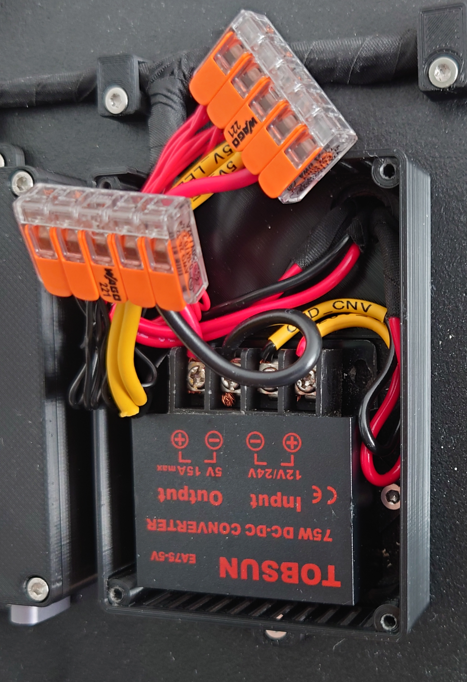
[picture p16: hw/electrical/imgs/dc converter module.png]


## Power relay

The purpose of power relay is to:
1. Delay poweroff (e.g. 30 seconds) to allow graceful shutdown of the `compute` module (Orange Pi)
2. Short protection (fuse)
3. 20 V power distribution box

As this relay will be always powered on (even if the wheel is switched off) a good quality off the shelf timer relay is used (`Relpol RPC-1ER-UNI`) to lower the risk of possible malfunctions. Timer relay is programmed to delay power off by 30 seconds and to delay power on for 2 seconds.

There is a separate wiring diagram for power relay module in the bottom right corner of the diagram. It describes how to connect together timer relay, fuse and power switch. For connections, WAGO connectors are used.

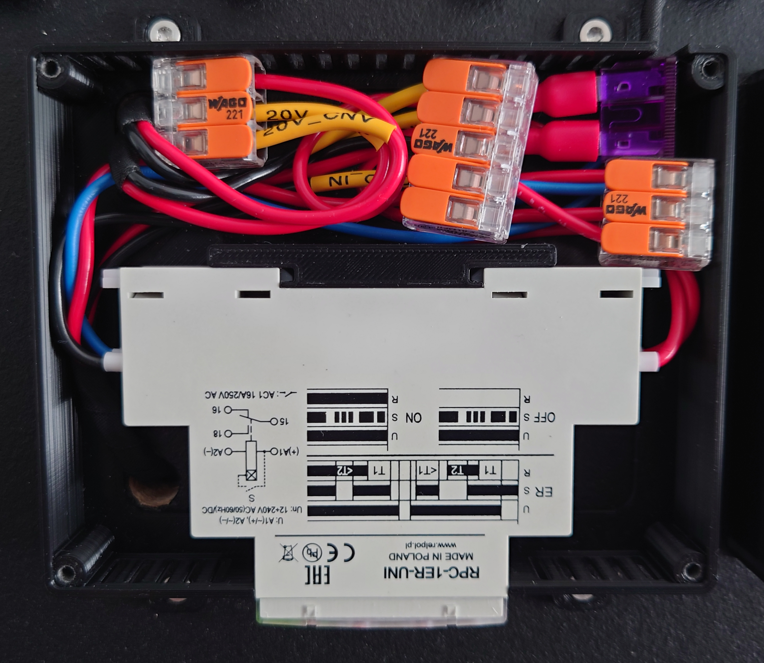
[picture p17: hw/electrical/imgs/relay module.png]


## Power supply

It is recommended to use at least 90 W power supply (19 - 24 V). In this case, `XT30` connector is used for easy replacement of the power supply.

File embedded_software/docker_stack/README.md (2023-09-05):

# Docker Stack for Wheel of Fortune

## Overview

This docker-compose stack provides a convenient way to run the Wheel of Fortune software on embedded computers, such as OrangePi 3 LTS. The stack consists of two containers:
  1. **Wheel of Fortune Container**: This container includes the Wheel of Fortune software.
  2. **Traefik Container**: Traefik is utilized as a reverse proxy to expose the user interface (UI) and the WLED interface. Traefik also provides authentication via Basic HTTP authentication.

## Usage

### Data folder

Copy example data from `wheel-of-fortune/example-data` to `~/data/wheel-of-fortune`. Make necessary changes to the data files.

### Docker stack

Copy/Link `wheel-of-fortune/embedded_software/docker_stack` to `~/docker_stack`.

Add `~/docker_stack/.env` file using following example:

```bash
DOMAIN_NAME=wheel.example.com
INTERNAL_DOMAIN_NAME=wheel.int.example.com
DATA_DIR=/home/orangepi/data

# Variables for Letsencrypt ACME DNS challenge (Cloudflare in this example)
LETSENCRYPT_EMAIL=
CLOUDFLARE_EMAIL=
CLOUDFLARE_DNS_API_TOKEN=

# Wheel of Fortune configuration
WHEEL_NAME=test-wheel
WHEEL_DISPLAY_NAME="Wheel of Fortune"
WHEEL_WLED_URL=
WHEEL_WLED_SEGMENTS='[
    {"name": "ambilight", "start": 0, "stop": 133},
    {"name": "logo", "start": 133, "stop": 170},
    {"name": "wheel", "start": 170, "stop": 205}
]'

# Wheel influxdb metrics
WHEEL_INFLUXDB_URL=https://influxdb.int.example.com
WHEEL_INFLUXDB_TOKEN=
WHEEL_INFLUXDB_ORG=wheelmetrics
WHEEL_INFLUXDB_BUCKET=wheel-of-fortune

# Traefik influxdb metrics
TRAEFIK_INFLUXDB_URL=https://influxdb.int.example.com
TRAEFIK_INFLUXDB_TOKEN=
TRAEFIK_INFLUXDB_ORG=wheelmetrics
TRAEFIK_INFLUXDB_BUCKET=traefik
```

Fill in any missing values and/or make necessary changes to `docker-compose.yml` file.

Add `usersfile` to `config/traefik` folder to list Basic Auth users.
For more information see https://doc.traefik.io/traefik/middlewares/http/basicauth/#usersfile

### Deploy

Start docker stack by

```bash
cd ~/docker_stack
docker compose up -d
```

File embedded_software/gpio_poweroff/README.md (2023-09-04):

# GPIO Poweroff

## Overview

This is a simple service designed to poll a GPIO pin for a poweroff signal. Currently, pin `PL08` (16) is assigned for detecting the shutdown signal. Please ensure that a pull-up resistor is installed.

During regular operation, the pin should remain in a low state. A transition to the high state will trigger the system to initiate a poweroff sequence.

## Installation

Copy Service Files to /opt:

```bash
sudo cp -r ~/wheel-of-fortune/embedded_software/gpio_poweroff /opt/
```

Enable and Start the Service:

```bash
sudo systemctl enable /opt/gpio_poweroff/gpio-poweroff.service
sudo systemctl start gpio-poweroff.service
```

Check Service Status:

```bash
sudo systemctl status gpio-poweroff.service
```

Remember to ensure that the `gpio-poweroff-script.sh` script is properly configured to poll the GPIO pin and trigger the poweroff sequence as needed.

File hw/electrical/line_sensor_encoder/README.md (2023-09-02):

## Line sensor encoder

Back                                        |  Front
:------------------------------------------:|:------------------------------------------:
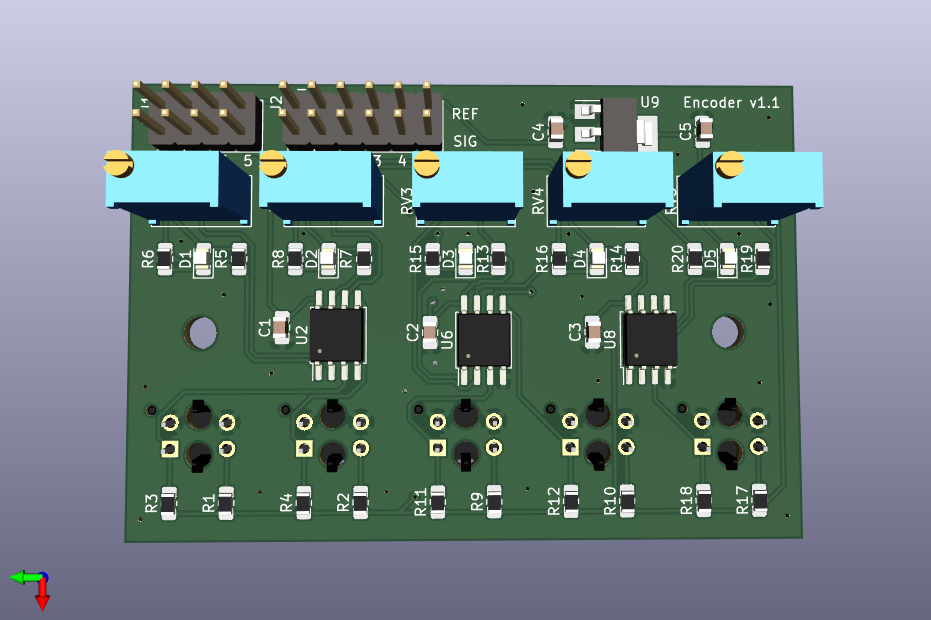
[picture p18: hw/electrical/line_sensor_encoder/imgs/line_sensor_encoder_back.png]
back
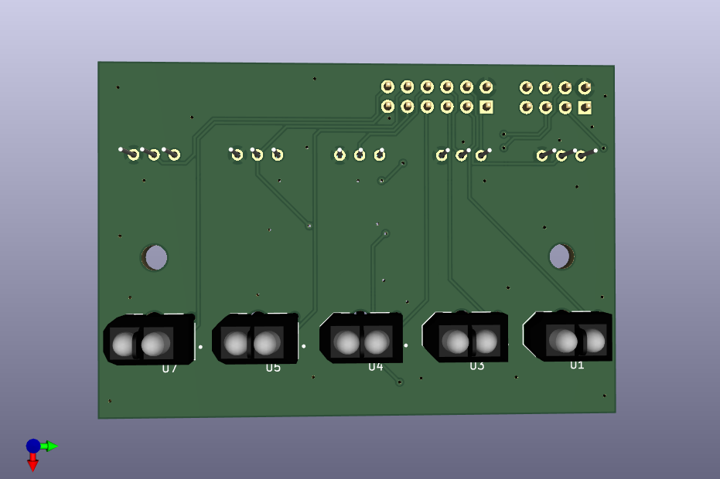
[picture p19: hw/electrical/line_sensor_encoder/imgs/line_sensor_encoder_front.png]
front
  |  

Custom encoder PCB for detecting absolute position of the wheel.
It consists of 5 `TCRT5000L` line sensors combined with voltage comparators
to have five binary outputs.

[PDF schematic](line_sensor_encoder.pdf)

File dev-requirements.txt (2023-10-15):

#
# This file is autogenerated by pip-compile with Python 3.10
# by the following command:
#
#    pip-compile --extra=dev --output-file=dev-requirements.txt pyproject.toml
#
aiocsv==1.2.4
    # via influxdb-client
aiodns==3.1.0
    # via wheel-of-fortune (pyproject.toml)
aiofiles==23.2.1
    # via wheel-of-fortune (pyproject.toml)
aiohttp==3.8.6
    # via
    #   influxdb-client
    #   wheel-of-fortune (pyproject.toml)
aiosignal==1.3.1
    # via aiohttp
annotated-types==0.6.0
    # via pydantic
anyio==3.7.1
    # via
    #   fastapi
    #   starlette
    #   watchfiles
async-timeout==4.0.3
    # via aiohttp
attrs==23.1.0
    # via aiohttp
black==23.9.1
    # via wheel-of-fortune (pyproject.toml)
build==1.0.3
    # via pip-tools
certifi==2023.7.22
    # via influxdb-client
cffi==1.16.0
    # via pycares
charset-normalizer==3.3.0
    # via aiohttp
click==8.1.7
    # via
    #   black
    #   pip-tools
    #   uvicorn
coloredlogs==15.0.1
    # via wheel-of-fortune (pyproject.toml)
exceptiongroup==1.1.3
    # via
    #   anyio
    #   pytest
fastapi==0.103.2
    # via wheel-of-fortune (pyproject.toml)
flake8==6.1.0
    # via wheel-of-fortune (pyproject.toml)
frozenlist==1.4.0
    # via
    #   aiohttp
    #   aiosignal
h11==0.14.0
    # via uvicorn
httptools==0.6.0
    # via uvicorn
humanfriendly==10.0
    # via coloredlogs
idna==3.4
    # via
    #   anyio
    #   yarl
influxdb-client[async]==1.38.0
    # via wheel-of-fortune (pyproject.toml)
iniconfig==2.0.0
    # via pytest
mccabe==0.7.0
    # via flake8
mergedeep==1.3.4
    # via wheel-of-fortune (pyproject.toml)
multidict==6.0.4
    # via
    #   aiohttp
    #   yarl
mypy-extensions==1.0.0
    # via black
opi-gpio==0.5.2
    # via wheel-of-fortune (pyproject.toml)
packaging==23.2
    # via
    #   black
    #   build
    #   pytest
pathspec==0.11.2
    # via black
pip-tools==7.3.0
    # via wheel-of-fortune (pyproject.toml)
platformdirs==3.11.0
    # via black
pluggy==1.3.0
    # via pytest
pycares==4.4.0
    # via aiodns
pycodestyle==2.11.1
    # via flake8
pycparser==2.21
    # via cffi
pydantic==2.4.2
    # via
    #   fastapi
    #   pydantic-settings
pydantic-core==2.10.1
    # via pydantic
pydantic-settings==2.0.3
    # via wheel-of-fortune (pyproject.toml)
pydub==0.25.1
    # via wheel-of-fortune (pyproject.toml)
pyflakes==3.1.0
    # via flake8
pygame==2.5.2
    # via wheel-of-fortune (pyproject.toml)
pyproject-hooks==1.0.0
    # via build
pytest==7.4.2
    # via wheel-of-fortune (pyproject.toml)
python-dateutil==2.8.2
    # via influxdb-client
python-dotenv==1.0.0
    # via
    #   pydantic-settings
    #   uvicorn
    #   wheel-of-fortune (pyproject.toml)
pyyaml==6.0.1
    # via
    #   uvicorn
    #   wheel-of-fortune (pyproject.toml)
reactivex==4.0.4
    # via influxdb-client
six==1.16.0
    # via python-dateutil
sniffio==1.3.0
    # via anyio
starlette==0.27.0
    # via fastapi
tomli==2.0.1
    # via
    #   black
    #   build
    #   pip-tools
    #   pyproject-hooks
    #   pytest
typing-extensions==4.8.0
    # via
    #   black
    #   fastapi
    #   pydantic
    #   pydantic-core
    #   reactivex
    #   uvicorn
urllib3==2.0.6
    # via influxdb-client
uvicorn[standard]==0.23.2
    # via wheel-of-fortune (pyproject.toml)
uvloop==0.18.0
    # via uvicorn
watchfiles==0.21.0
    # via uvicorn
websockets==11.0.3
    # via uvicorn
wheel==0.41.2
    # via pip-tools
yarl==1.9.2
    # via aiohttp

# The following packages are considered to be unsafe in a requirements file:
# pip
# setuptools

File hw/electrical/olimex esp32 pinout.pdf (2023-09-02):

pin | name | comment | connected to
1 | 5V | | 5V
2 | 3.3V
3 | GND | | GND
4 | ESP_EN | reset
5 | GPIO0 | boot pin
6 | GPIO1 | UART
7 | GPIO2 | 2.2k pullup
8 | GPIO3 | UART
9 | GPIO4 | OK | LED1
10 | GPIO5 | 10k pullup | LED2
1 | GPI39 | input only, ext power sense
2 | GPI36 | input only, 10k pullup | ENC1
3 | GPI35 | input only, opt battery | ENC2
4 | GPI34 | input only, button, 10k pullup
5 | GPIO33 | ok | ENC3
6 | GPIO32 | ok | ENC4
7 | GPIO16 | 2.2k pullup | ENC5
8 | GPIO15 | 10k pullup | SERVO1
9 | GPIO14 | OK | SERVO2
10 | GPIO13 | 2.2k pullup | SERVO3

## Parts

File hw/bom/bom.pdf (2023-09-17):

sub-assembly | type | name | quantity | url
audio | 3D printed part | amplifier mount | 1
audio | 3D printed part | amplifier cover | 1
audio | screw | DIN912 M3x6 | 4
audio | screw | wood screw 3x20 torx | 2
audio | device | amplifier A502S TPA3116D2 50W | | 1 https://vi.aliexpress.com/item/1005003447250822.html
audio | device | kebidumei ground loop isolator | | 1 https://vi.aliexpress.com/item/1005001604545947.html
audio | cable | audio cable flat 20cm | | 1 https://vi.aliexpress.com/item/10000360130480.html
compute | 3D printed part | compute mount | 1
compute | 3D printed part | compute cover | 1
compute | screw | DIN912 M3x6 | 4
compute | screw | wood screw 3x20 torx | 4
compute | device | Orange PI 3 LTS | | 1 http://www.orangepi.org/html/hardWare/computerAndMicrocontrollers/detail
compute | device | Olimex ESP32 POE | | 1 https://www.olimex.com/Products/IoT/ESP32/ESP32-POE/open-source-
compute | screw | D84 M3x5 | 4
compute | screw | D84 M2x5 | 3
compute | washer | nylon M3 | 4
compute | washer | nylon M2 | 3
compute | cable | usb bend UC-095F | | 1 https://vi.aliexpress.com/item/1005005200683069.html
compute | cable | ethernet cable Left-Right, 25cm | | 1 https://vi.aliexpress.com/item/1005002782553550.html
dc-converter | 3D printed part | dc converter mount
dc-converter | 3D printed part | dc converter cover
dc-converter | dc-converter | TOBSUN 12V 24V TO 5V 15A | | 1 https://vi.aliexpress.com/item/4001107349411.html
dc-converter | connector | WAGO 221-415 | 2
dc-converter | screw | DIN912 M3x6 | 4
dc-converter | screw | wood screw 3x20 torx | 4
encoder | 3D printed part | encoder mount | 1
encoder | screw | wood screw 4x40 torx | 2
encoder | sensor | line sensor TCRT5000L | 5
encoder | pcb | JLCPCB manufacturing (5 pcb) | 1
encoder | potentiometer | 3296W 10k | 5
encoder | comparator | LM393ADT | 5
encoder | screw | DIN912 M3x5 | 2

encoder | washer | nylon washer M3 | 2
flipper | 3D printed part | flipper mount | 1
flipper | 3D printed part | flipper fixed spring cover | 1
flipper | 3D printed part | flipper damper | 1
flipper | 3D printed part | flipper inset | 1
flipper | 3D printed part | flipper bumper | 1
flipper | screw | ISO10642 M4x10 | 4
flipper | screw | ISO7380 M4x12 | 2
flipper | washer | DIN125 M4 | 1
flipper | standoff | Wurth 970700471 M4x70 | 1 https://ee.farnell.com/wurth-elektronik/970700471/abstandhalt-6kant-innen-
flipper | bearing hub | MT164-624ZZ-10-4 | 1 https://vi.aliexpress.com/item/33010273520.html
flipper rubber band | | 1
flipper damper | leather | 1
flipper | spring | 10x42x0.9 mm | 1
flipper | screw | wood screw torx 4x40 | 5
limit wheel | 3D printed part | limit wheel mount | 6
limit wheel | washer | DIN125 M5 | 12
limit wheel | screw | ISO10642 M5x20 | 6
limit wheel | wheel | 3D printed part printer wheels 625ZZ | 6 https://vi.aliexpress.com/item/1005003786298839.html
limit wheel | screw | wood screw 3x20 torx | 12
power relay | 3D printed part | relay mount | 1
power relay | 3D printed part | relay mount cover | 1
power relay | screw | DIN912 M3x6 | 4
power relay | screw | wood screw 3x20 torx | 4
power relay | time relay | Relpol RPC-1ER-UNI | 1 https://www.sakt.ee/en/time-relays/8872-rpc-1er-uni-time-relay-12-240acdc-
power relay | fuse | 4A car fuse | 1
power relay | connector | WAGO 221-413 | 2
power relay | connector | WAGO 221-415 | 1
power switch | 3D printed part | power switch mount | 1
power switch | switch | DPST MRS201-3C3 | 1 https://www.oomipood.ee/product/mrs201_3c3_klahvluliti_2_on_off_3a_250v
power switch | screw | wood screw torx 3x25 | 2
linear actuator | 3D printed part | gear | 3
linear actuator | 3D printed part | logo mount | 3

linear actuator | 3D printed part | railings | 3
linear actuator | 3D printed part | gear rack | 3
linear actuator | 3D printed part | demo logo | 4
linear actuator | servo | JX W4505-4T | 3
linear actuator | screw | wood screw torx 3x25 | 12
speaker | 3D printed part | speaker stud 1 | 2
speaker | 3D printed part | speaker stud 2 | 2
speaker | screws | flat head wood screw 4x25 | 4
speaker | speaker | Alpine SXE-0825S | 2 https://www.alpine.co.uk/p/Products/SingleView/SXE-0825S
backplate | wood | particle board / plywood 18 mm | 1
backplate | screw | ISO10642 M12x70 full thread | 1 https://vi.aliexpress.com/item/1005004860869917.html
backplate | washer | DIN440 M12 | 1
backplate | nut | DIN439 M12 | 1
backplate | 3D printed part | wire clip small | 57
backplate | 3D printed part | wire clip large | 3
backplate | 3D printed part | led strip clip | 12
backplate | screw | wood screw 3x20 torx | 72
backplate | led strip | WS2812, 3m back, 60 leds/m | 1
cover | 3D printed part | cover logo | 1
cover | 3D printed part | cover base | 1
cover | 3D printed part | cover led ring | 1
cover | 3D printed part | cover locker | 1
cover | 3D printed part | cover logo backlight | 1
cover | 3D printed part | cover mantle | 1
cover | led strip | 5mm Black WS2812, 1m, 120 leds/m | 1
cover | led strip | WS2812, 1m back, 60 leds/m | 1
cover | screw | ISO10642 M3x10 | 8
cover | screw | ISO10642 M3x16 | 8
cover | screw | DIN914 45H M3x6 | 3
wheel | 3D printed part | bearing hub ext | 1
wheel | washer | DIN7349 (5,3X15X2,0) | 16
wheel | screw | ISO10642 M5X30 | 16
wheel | pins | DIN7979 M5 8x60 | 16

wheel | washer | DIN125 M33 | 1
wheel | screw | ISO10642 M5X45 | 4
wheel | washer | DIN433 M12 | 1
wheel | washer | DIN125 M12 | 1
wheel | nut | DIN934 M12 | 1
wheel | bearing | SKF6201 | 2 https://www.stokker.ee/kuullaager-6201-2z-skf-c-6201%7C2z-skf
wheel | bearing hub | MT164-6201ZZ-15-12 | 1 https://vi.aliexpress.com/item/33010273520.html
wheel | wood | particle board / plywood 18 mm | 1
wheel | bearing | 605zz 5x14x5mm | 8 https://vi.aliexpress.com/item/1005003477513135.html
wiring | wire | 0.75 red H05VK075RT | 6
wiring | wire | 0.75 black H05VK075SW | 6
wiring | wire | 0.35 red FLRY-B0.35-BK | 8
wiring | wire | 0.35 red FLRY-B0.35-RD | 8
wiring | wire | 0.35 gray FLRY-B0.35-GY | 4
wiring | wire | 0.35 gray FLRY-B0.35-GR | 4
wiring | wire | 0.22 yellow FLRY-A0.22-YL | 4
wiring | connector | XT30U-F | 2
wiring | connector | XT30U-M | 2 https://www.oomipood.ee/product/67783_gby_3_5mm_stereo_otse_pistik_3
wiring | cable | audio cable 1m | 1
finish | permanent marker | white 2mm | 1 https://www.k-rauta.ee/p/veekindel-marker-2-mm-valge/e8xu
finish | blackboard paint | Tikkurila 0.3L | 1 https://www.k-rauta.ee/p/eriotstarbeline-varv-tikkurila/aju
finish | chalk markers | Liquid chalk Apli | 1 https://vunder.ee/en/product/liquid-chalk-apli/
power supply | power supply | 20V 90W | 1
power supply | extension coord | 3m XT30 | 1

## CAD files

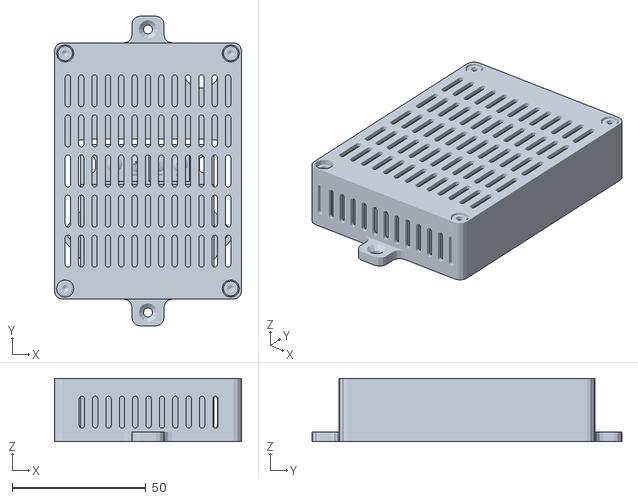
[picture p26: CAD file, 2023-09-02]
hw/mech/backplate/dc converter/dc converter assembly.STL
70.0 x 116.0 x 23.6

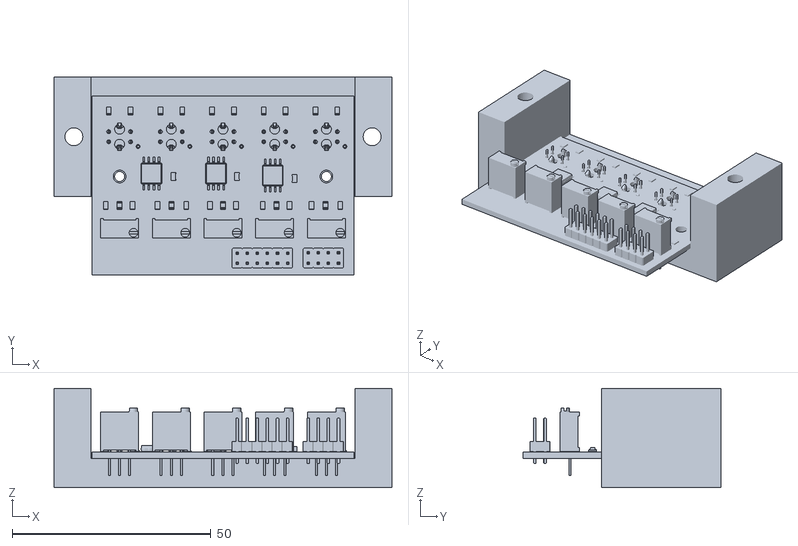
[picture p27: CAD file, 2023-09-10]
hw/mech/backplate/encoder/encoder assembly.STL
85.0 x 49.8 x 25.0

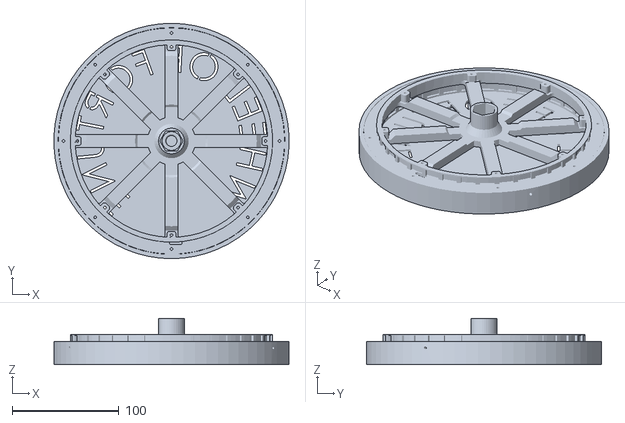
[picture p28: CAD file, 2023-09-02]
hw/mech/cover/cover assembly.STL
219.7 x 220.0 x 43.1

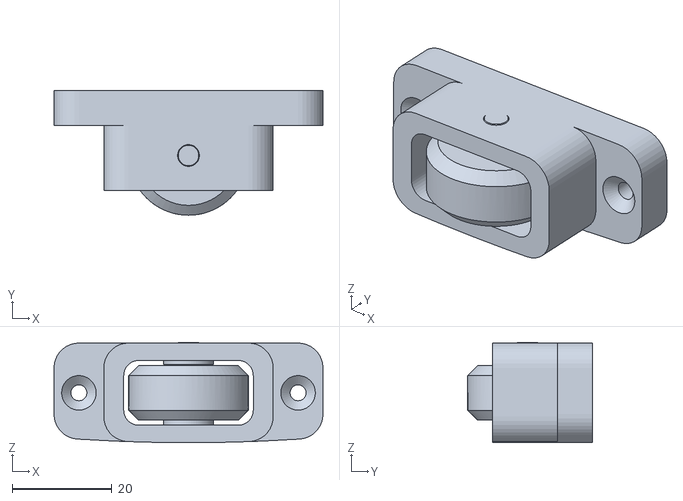
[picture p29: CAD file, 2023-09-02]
hw/mech/backplate/limit wheel/limit wheel assembly.STL
54.0 x 25.0 x 20.1

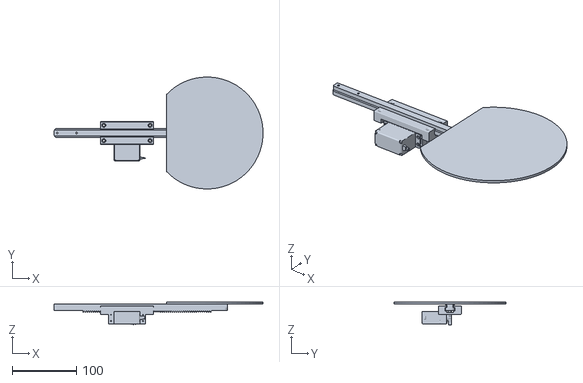
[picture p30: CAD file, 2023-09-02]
hw/mech/backplate/linear actuator/linear actuator assembly.STL
324.9 x 173.9 x 35.1

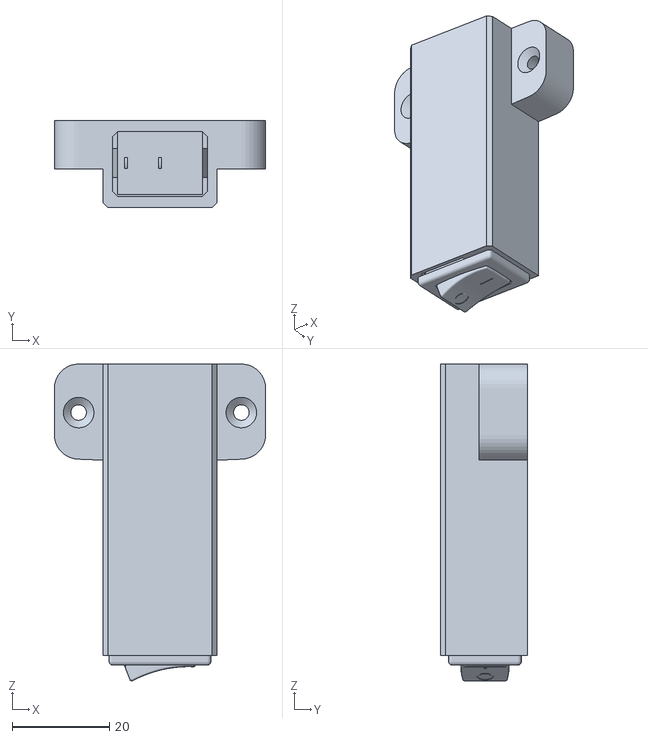
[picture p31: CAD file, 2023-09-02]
hw/mech/backplate/power switch/power switch assembly.STL
43.5 x 17.9 x 65.3

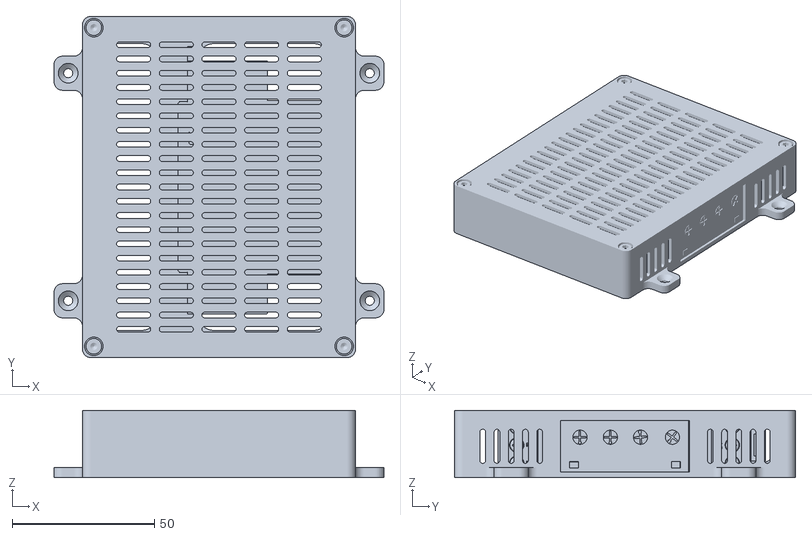
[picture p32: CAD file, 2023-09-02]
hw/mech/backplate/power relay/power relay assembly.STL
116.0 x 120.0 x 23.6

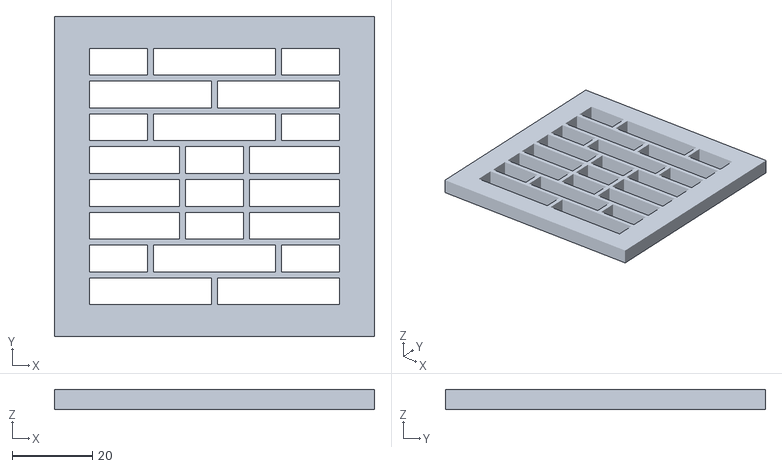
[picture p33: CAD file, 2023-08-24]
embedded_software/WLED/usermods/word-clock-matrix/Word Clock Baffle.stl
80.0 x 80.0 x 5.00

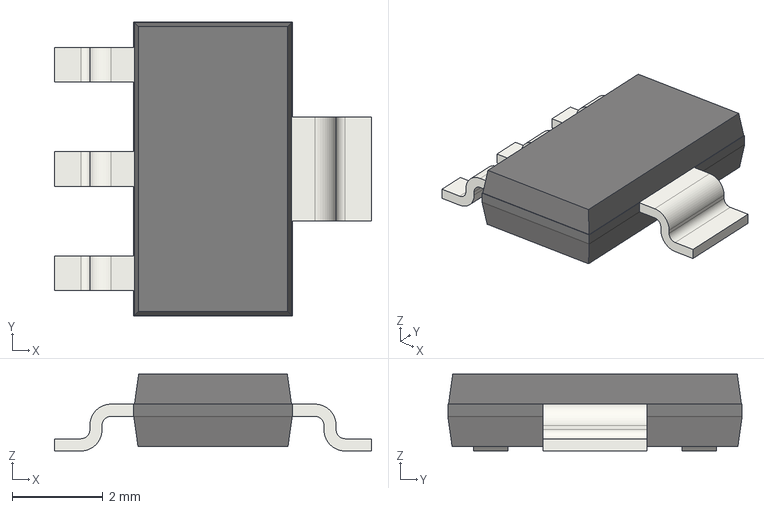
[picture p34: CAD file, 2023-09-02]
hw/electrical/line_sensor_encoder/3dmodels/SOT-223.step
7.00 x 6.50 x 1.70 mm

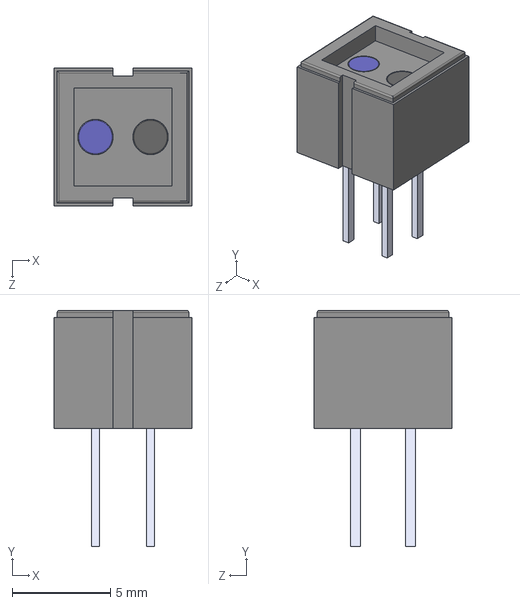
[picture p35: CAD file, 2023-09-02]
hw/electrical/line_sensor_encoder/symbols/TCRT5000L.step
7.00 x 12.0 x 7.00 mm

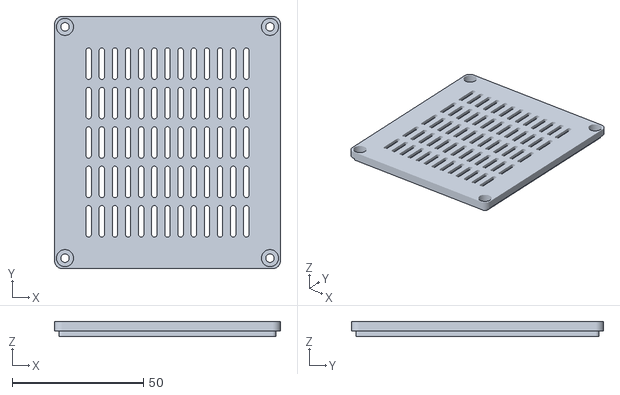
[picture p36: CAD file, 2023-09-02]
hw/mech/backplate/amplifier/amplifer cover.STL
86.0 x 96.0 x 5.60

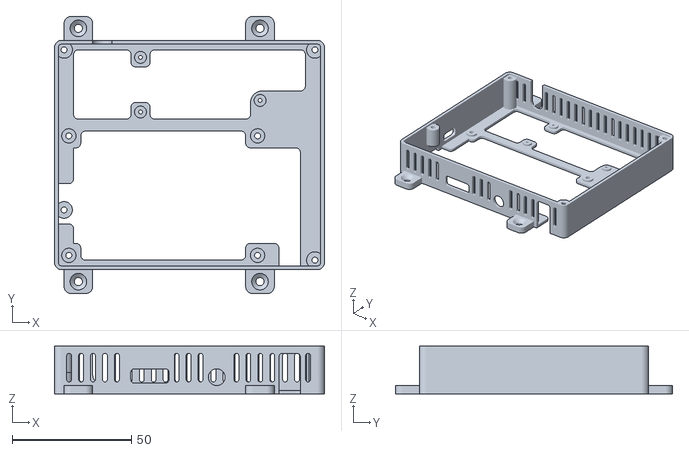
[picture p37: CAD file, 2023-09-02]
hw/mech/backplate/compute/compute mount.STL
113.0 x 116.0 x 20.0

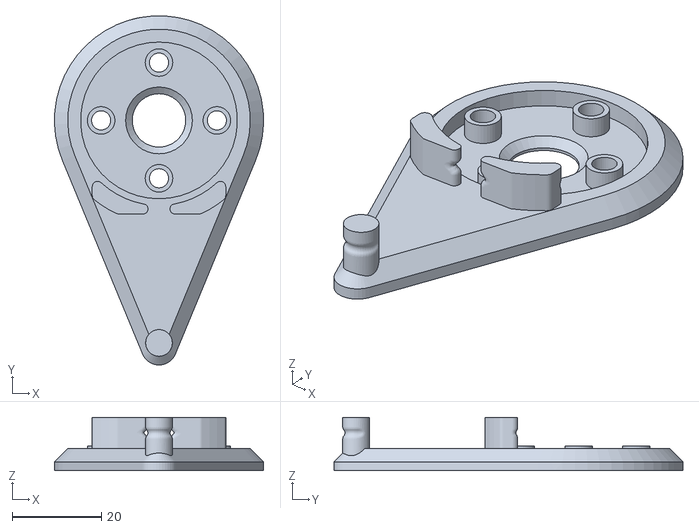
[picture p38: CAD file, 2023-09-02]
hw/mech/backplate/flipper/flipper inset.STL
47.0 x 78.4 x 12.0

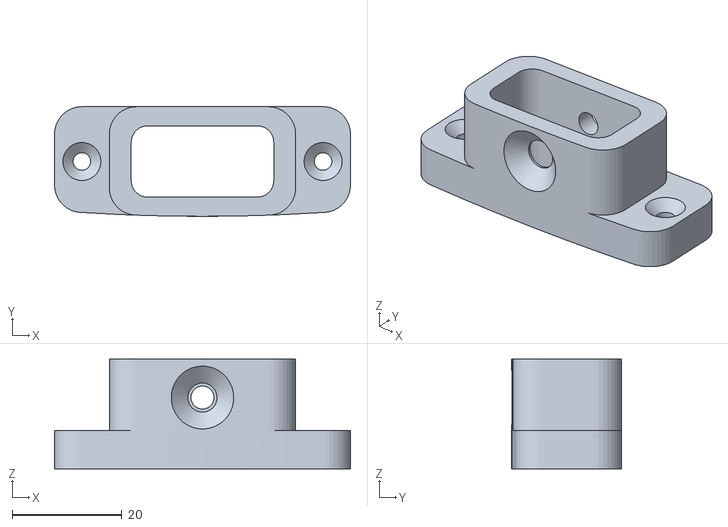
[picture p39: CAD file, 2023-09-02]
hw/mech/backplate/limit wheel/limit wheel mount.STL
54.0 x 20.0 x 20.0

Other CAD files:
hw/mech/backplate/linear actuator/demo logo.STL
hw/mech/backplate/power relay/relay cover.STL
hw/mech/backplate/power switch/switch mount.STL
hw/mech/backplate/speaker/speaker.STL
hw/electrical/line_sensor_encoder/3dmodels/C_0805_2012Metric.step
hw/electrical/line_sensor_encoder/3dmodels/LED_0805_2012Metric.step
hw/electrical/line_sensor_encoder/3dmodels/PinHeader_2x04_P2.54mm_Vertical.step
hw/electrical/line_sensor_encoder/3dmodels/PinHeader_2x06_P2.54mm_Vertical.step
hw/electrical/line_sensor_encoder/3dmodels/Potentiometer_Bourns_3296W_Vertical.step
hw/electrical/line_sensor_encoder/3dmodels/R_0805_2012Metric.step
hw/electrical/line_sensor_encoder/3dmodels/SSOP-8_5.25x5.24mm_P1.27mm.step
hw/electrical/line_sensor_encoder/3dmodels/TCRT5000.stp
hw/mech/backplate/amplifier/amplifer mount.STL
hw/mech/backplate/compute/compute cover.STL
hw/mech/backplate/dc converter/dc converter cover.STL
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

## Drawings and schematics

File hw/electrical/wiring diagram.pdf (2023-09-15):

## power (20V, fuse protected)

## sound

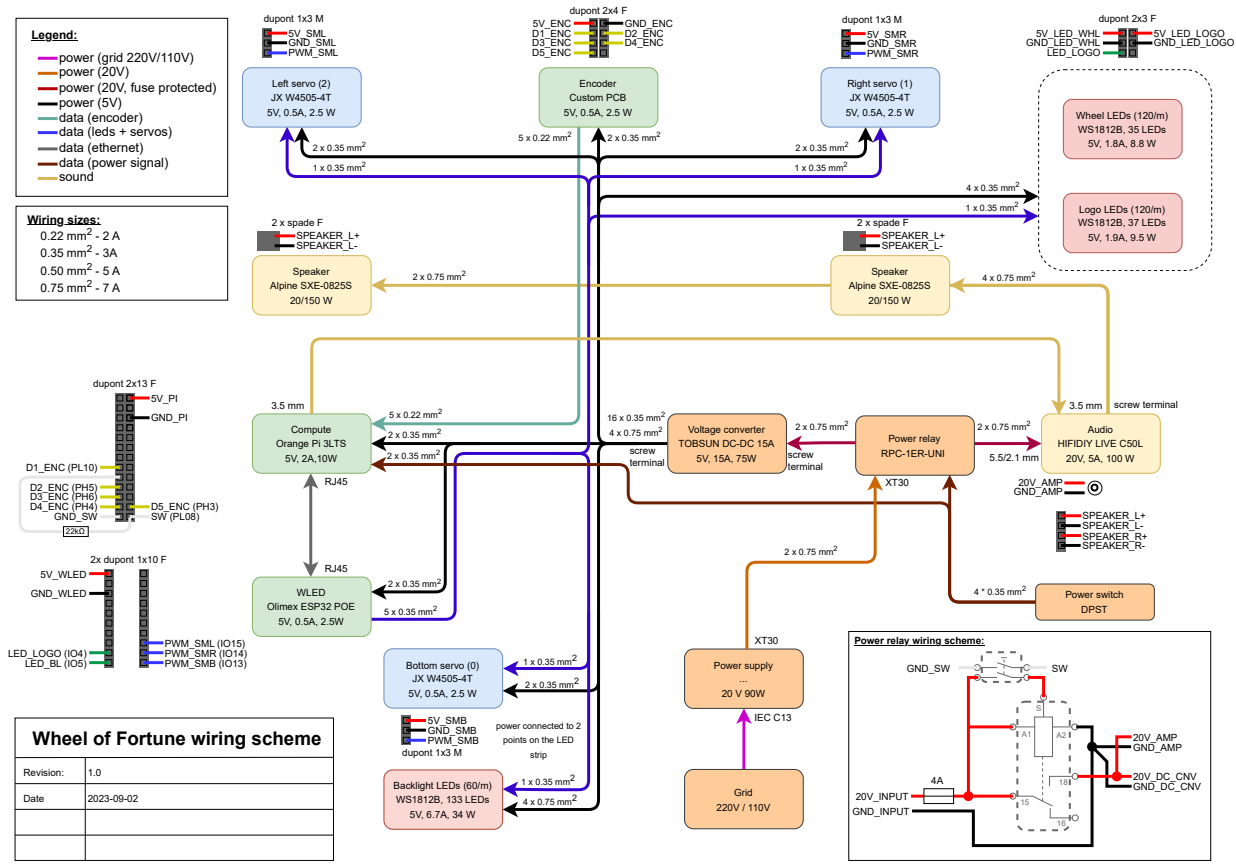
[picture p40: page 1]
2 x 0.75 mm²; Power supply ... 20 V 90W; 2 x 0.35 mm²; 16 x 0.35 mm²; 4 x 0.75 mm²; Audio HIFIDIY LIVE C50L 20V, 5A, 100 W; 5 x 0.22 mm²; Compute Orange Pi 3LTS 5V, 2A,10W; 5 x 0.35 mm²; WLED Olimex ESP32 POE 5V, 0.5A, 2.5W; Bottom servo (0) JX W4505-4T 5V, 0.5A, 2.5 W; 1 x 0.35 mm²; Left servo (2) JX W4505-4T 5V, 0.5A, 2.5 W; Right servo (1) JX W4505-4T 5V, 0.5A, 2.5 W; Backlight LEDs (60/m) WS1812B, 133 LEDs 5V, 6.7A, 34 W; Grid 220V / 110V; Encoder Custom PCB 5V, 0.5A, 2.5 W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

power (5V)
data (encoder)
data (leds + servos)
data (ethernet)
data (power signal)

Voltage converter
TOBSUN DC-DC 15A

Power relay wiring scheme:

Wheel of Fortune wiring scheme

power connected to 2
points on the LED
strip

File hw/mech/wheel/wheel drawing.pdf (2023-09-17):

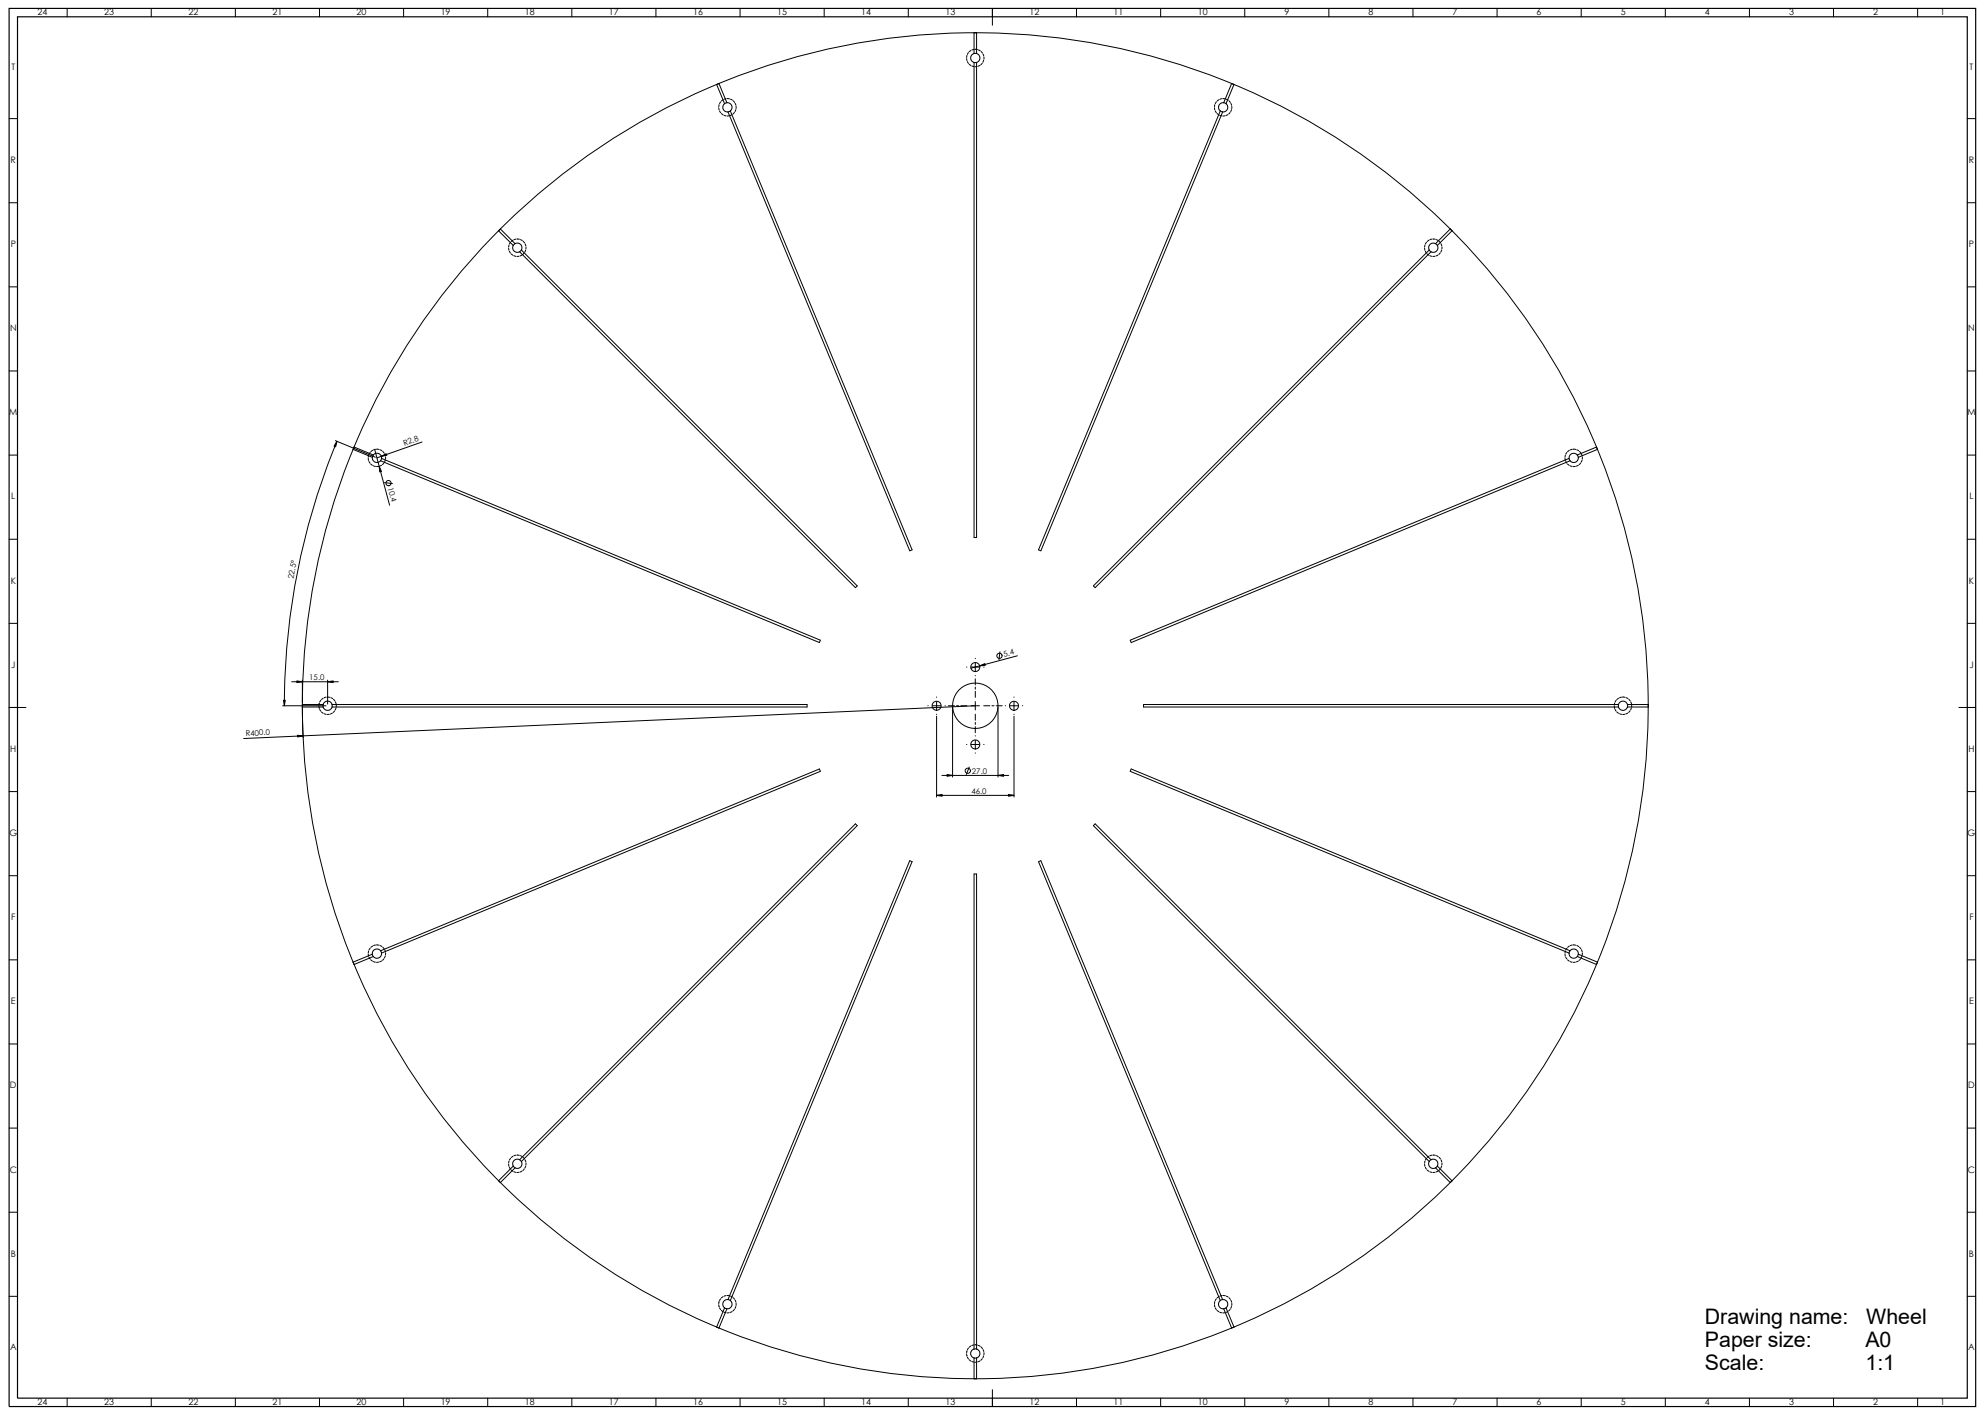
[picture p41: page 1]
Paper size:; Scale:

Drawing name: Wheel

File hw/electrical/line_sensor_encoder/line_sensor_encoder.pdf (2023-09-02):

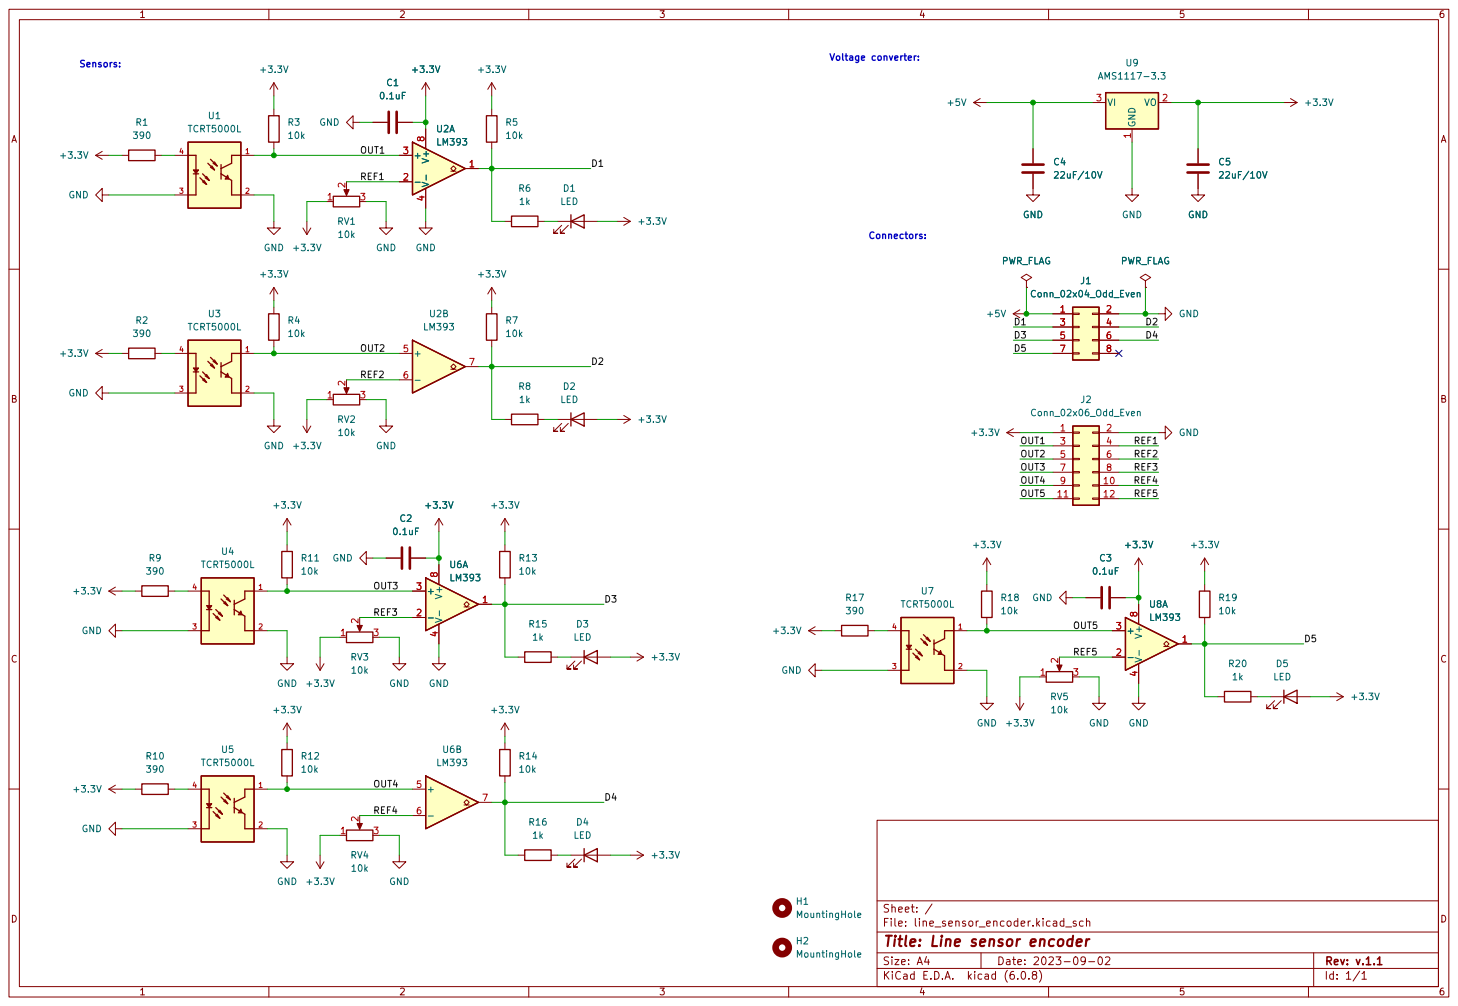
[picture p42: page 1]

File: line_sensor_encoder.kicad_sch Sheet: /
Id: 1/1 Title: Line sensor encoder

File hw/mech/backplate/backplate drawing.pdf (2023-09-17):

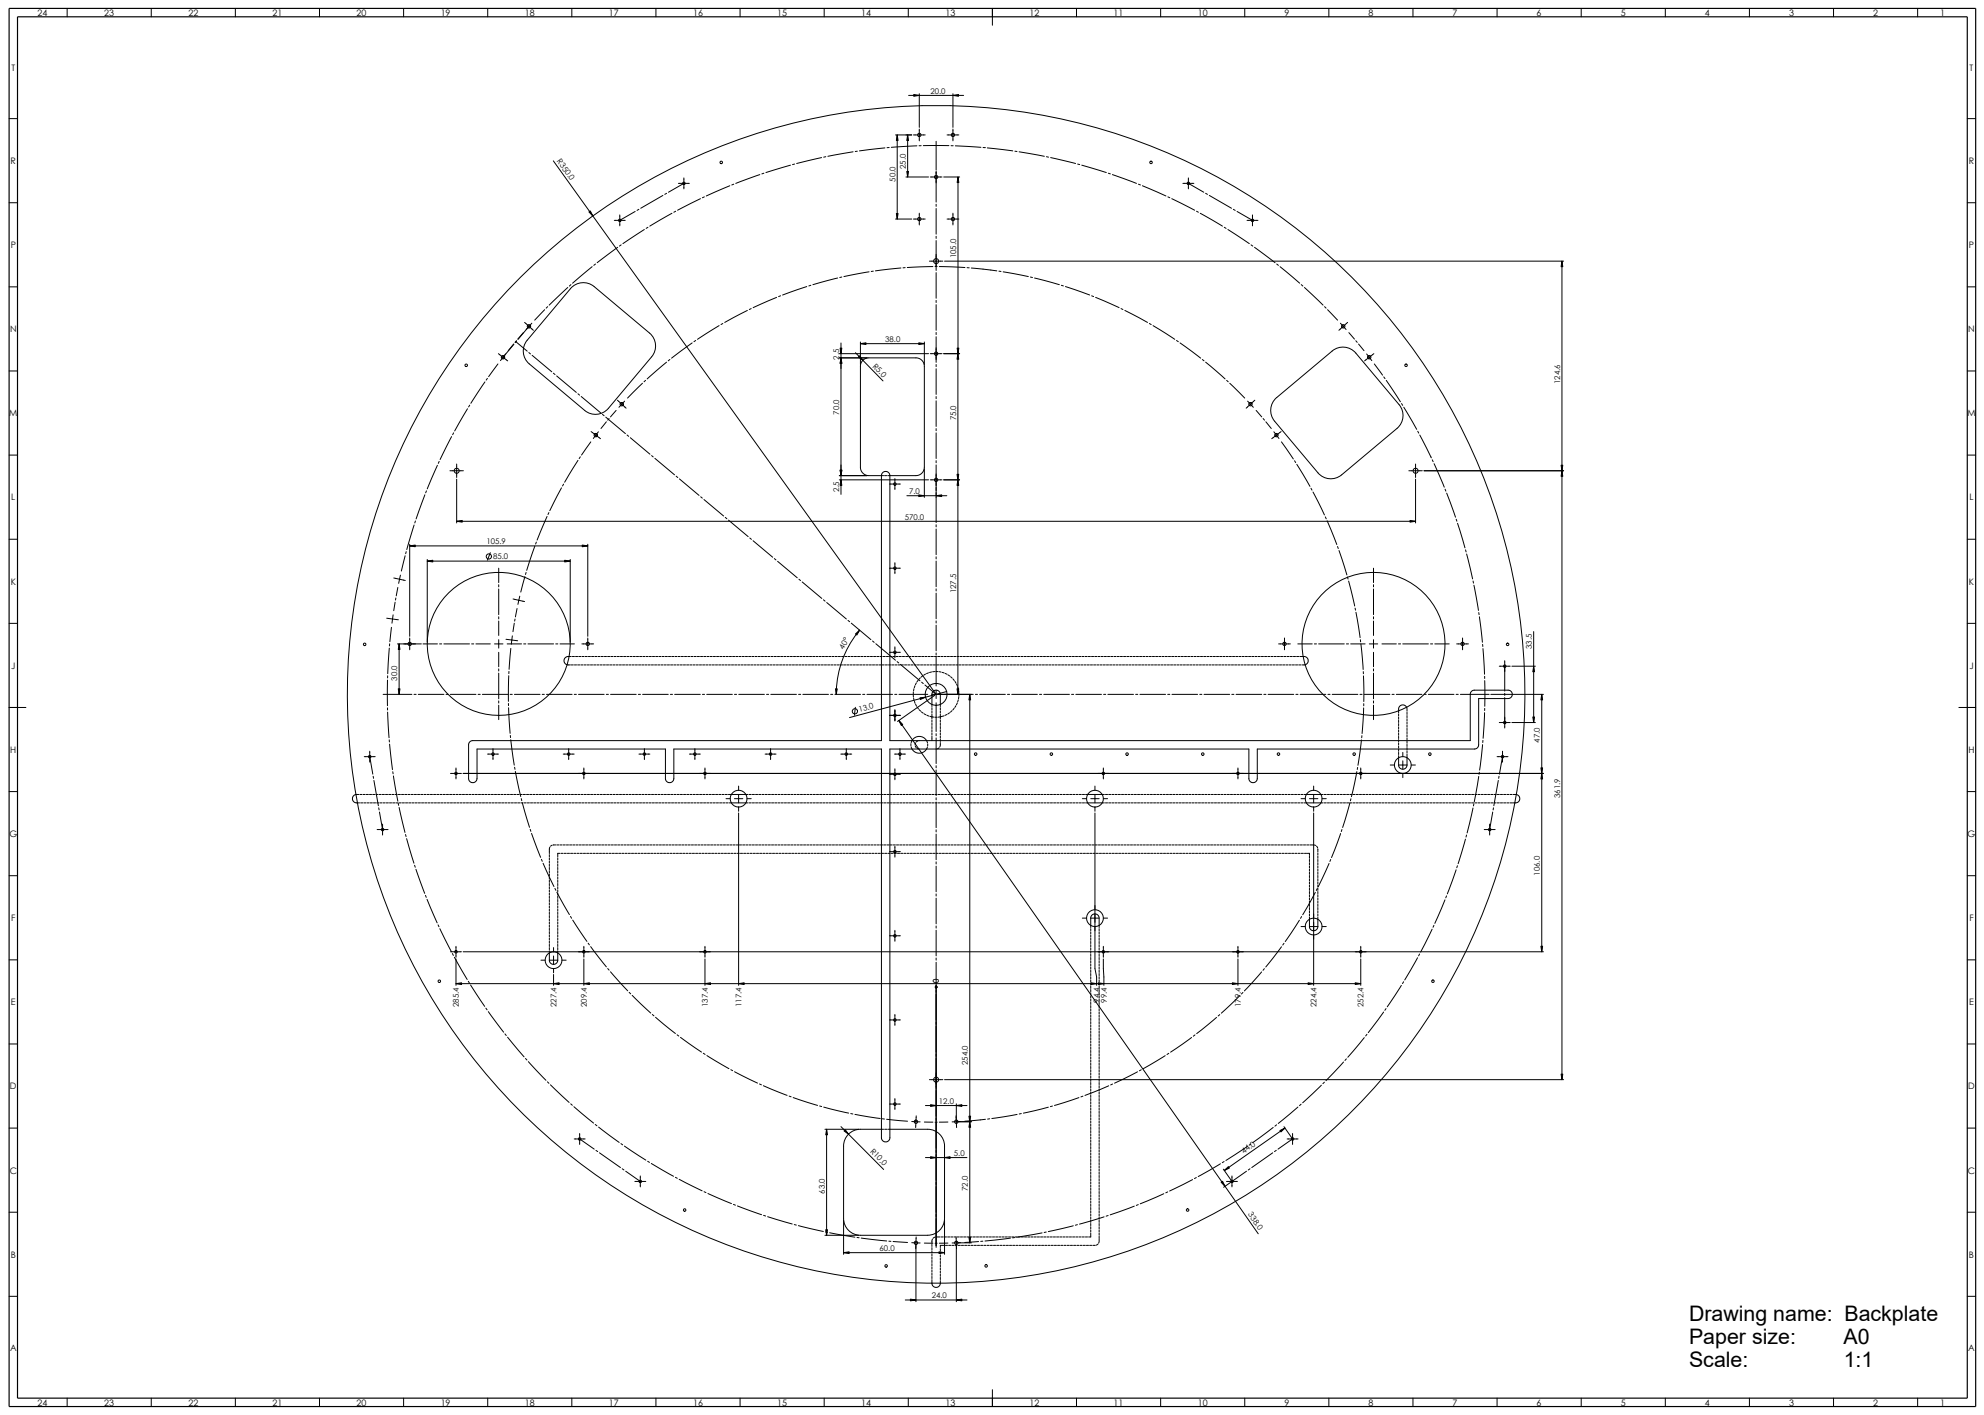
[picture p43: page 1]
Paper size:; Scale:

Drawing name: Backplate

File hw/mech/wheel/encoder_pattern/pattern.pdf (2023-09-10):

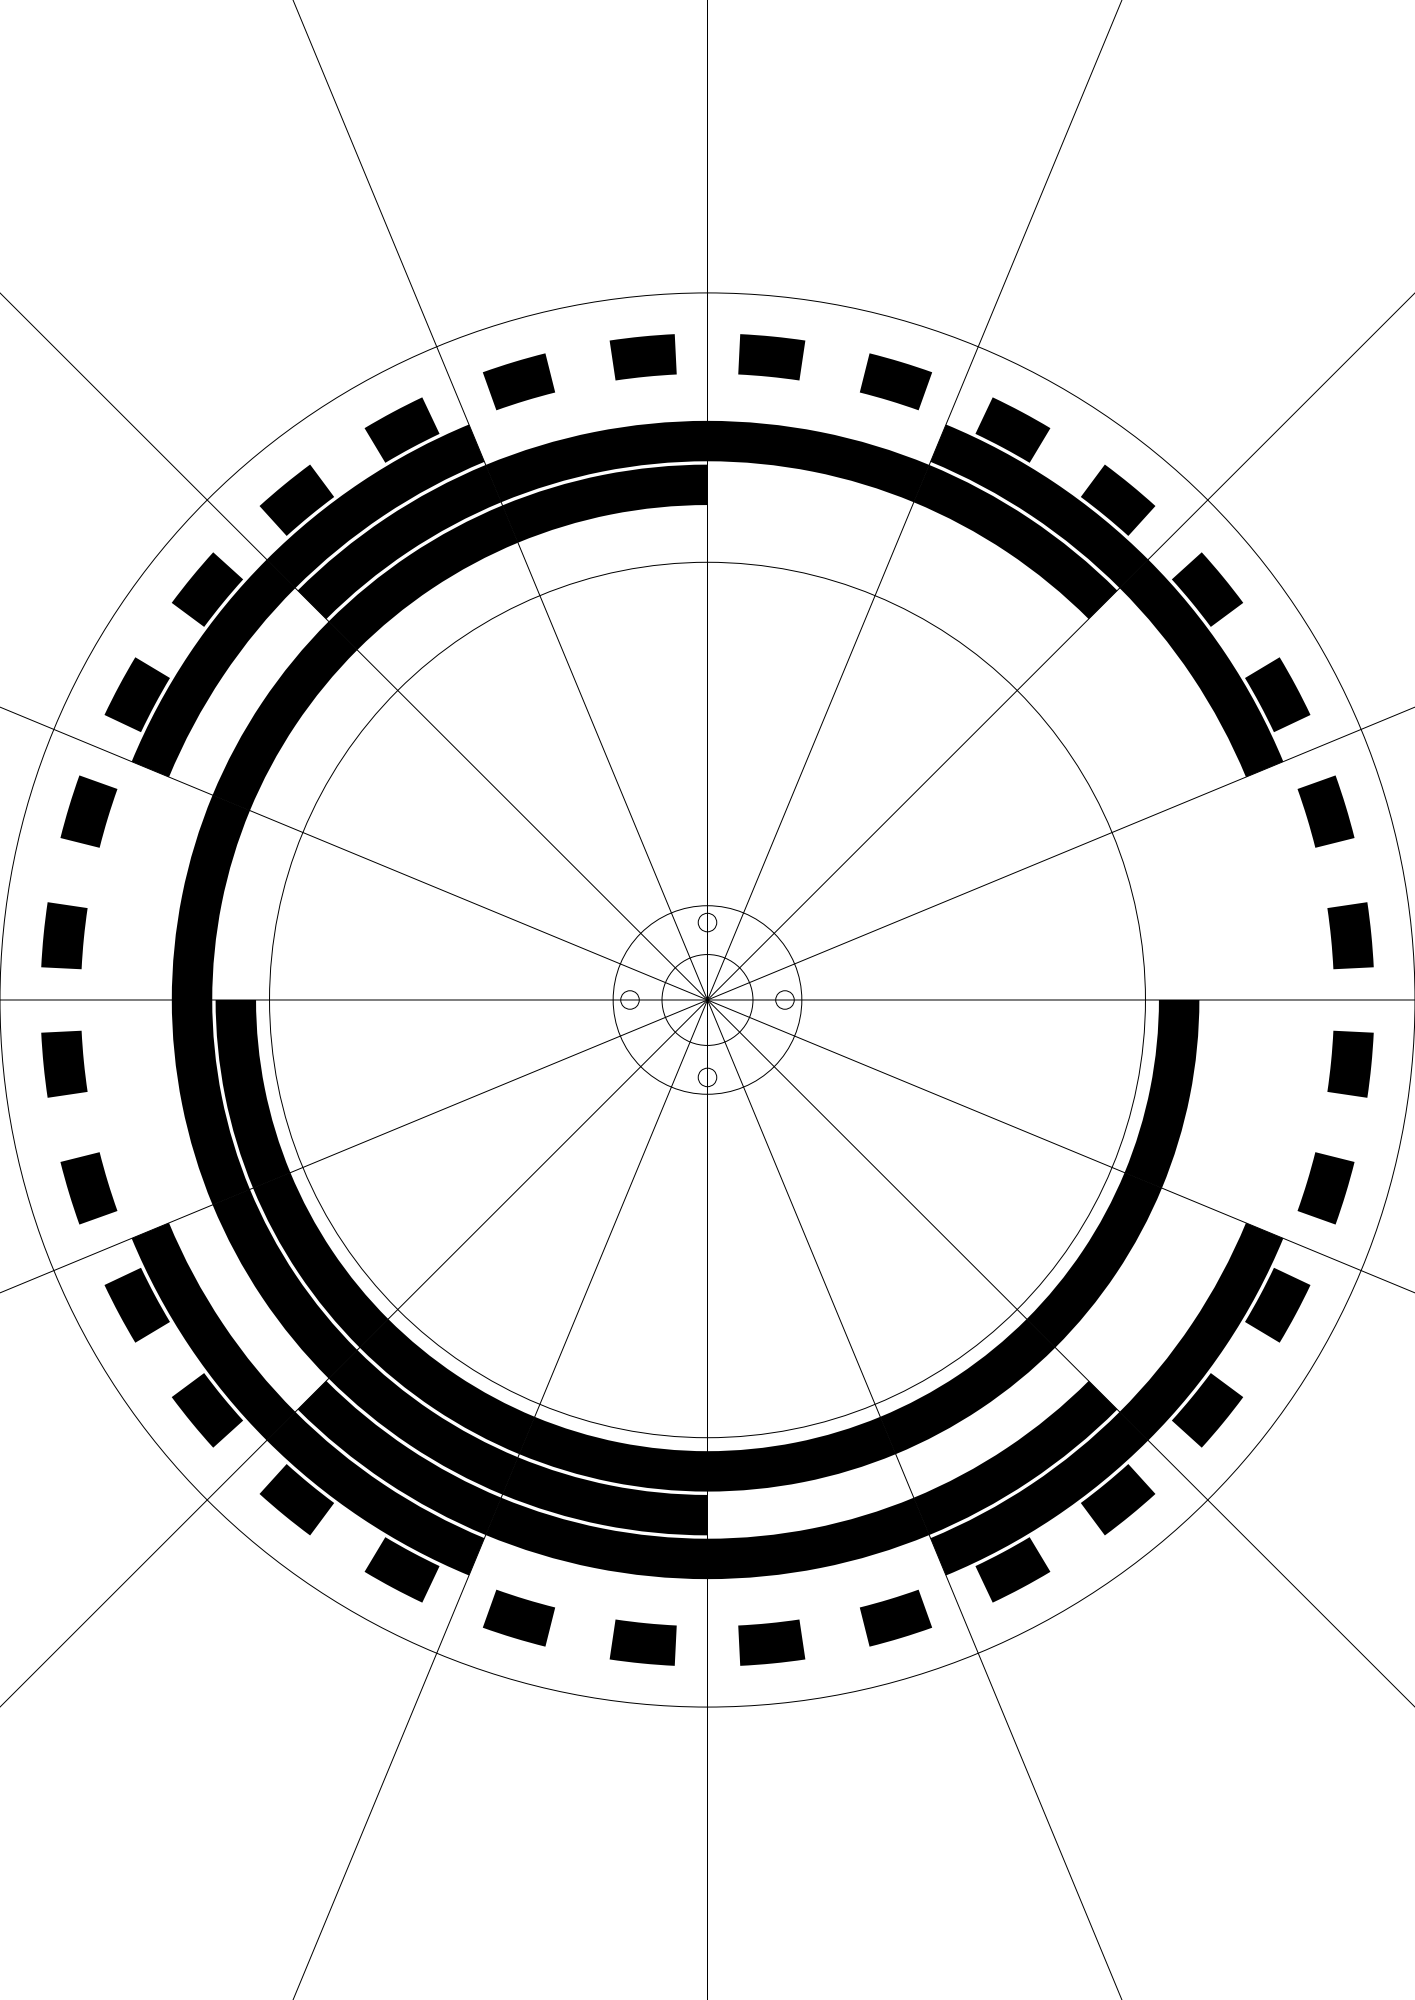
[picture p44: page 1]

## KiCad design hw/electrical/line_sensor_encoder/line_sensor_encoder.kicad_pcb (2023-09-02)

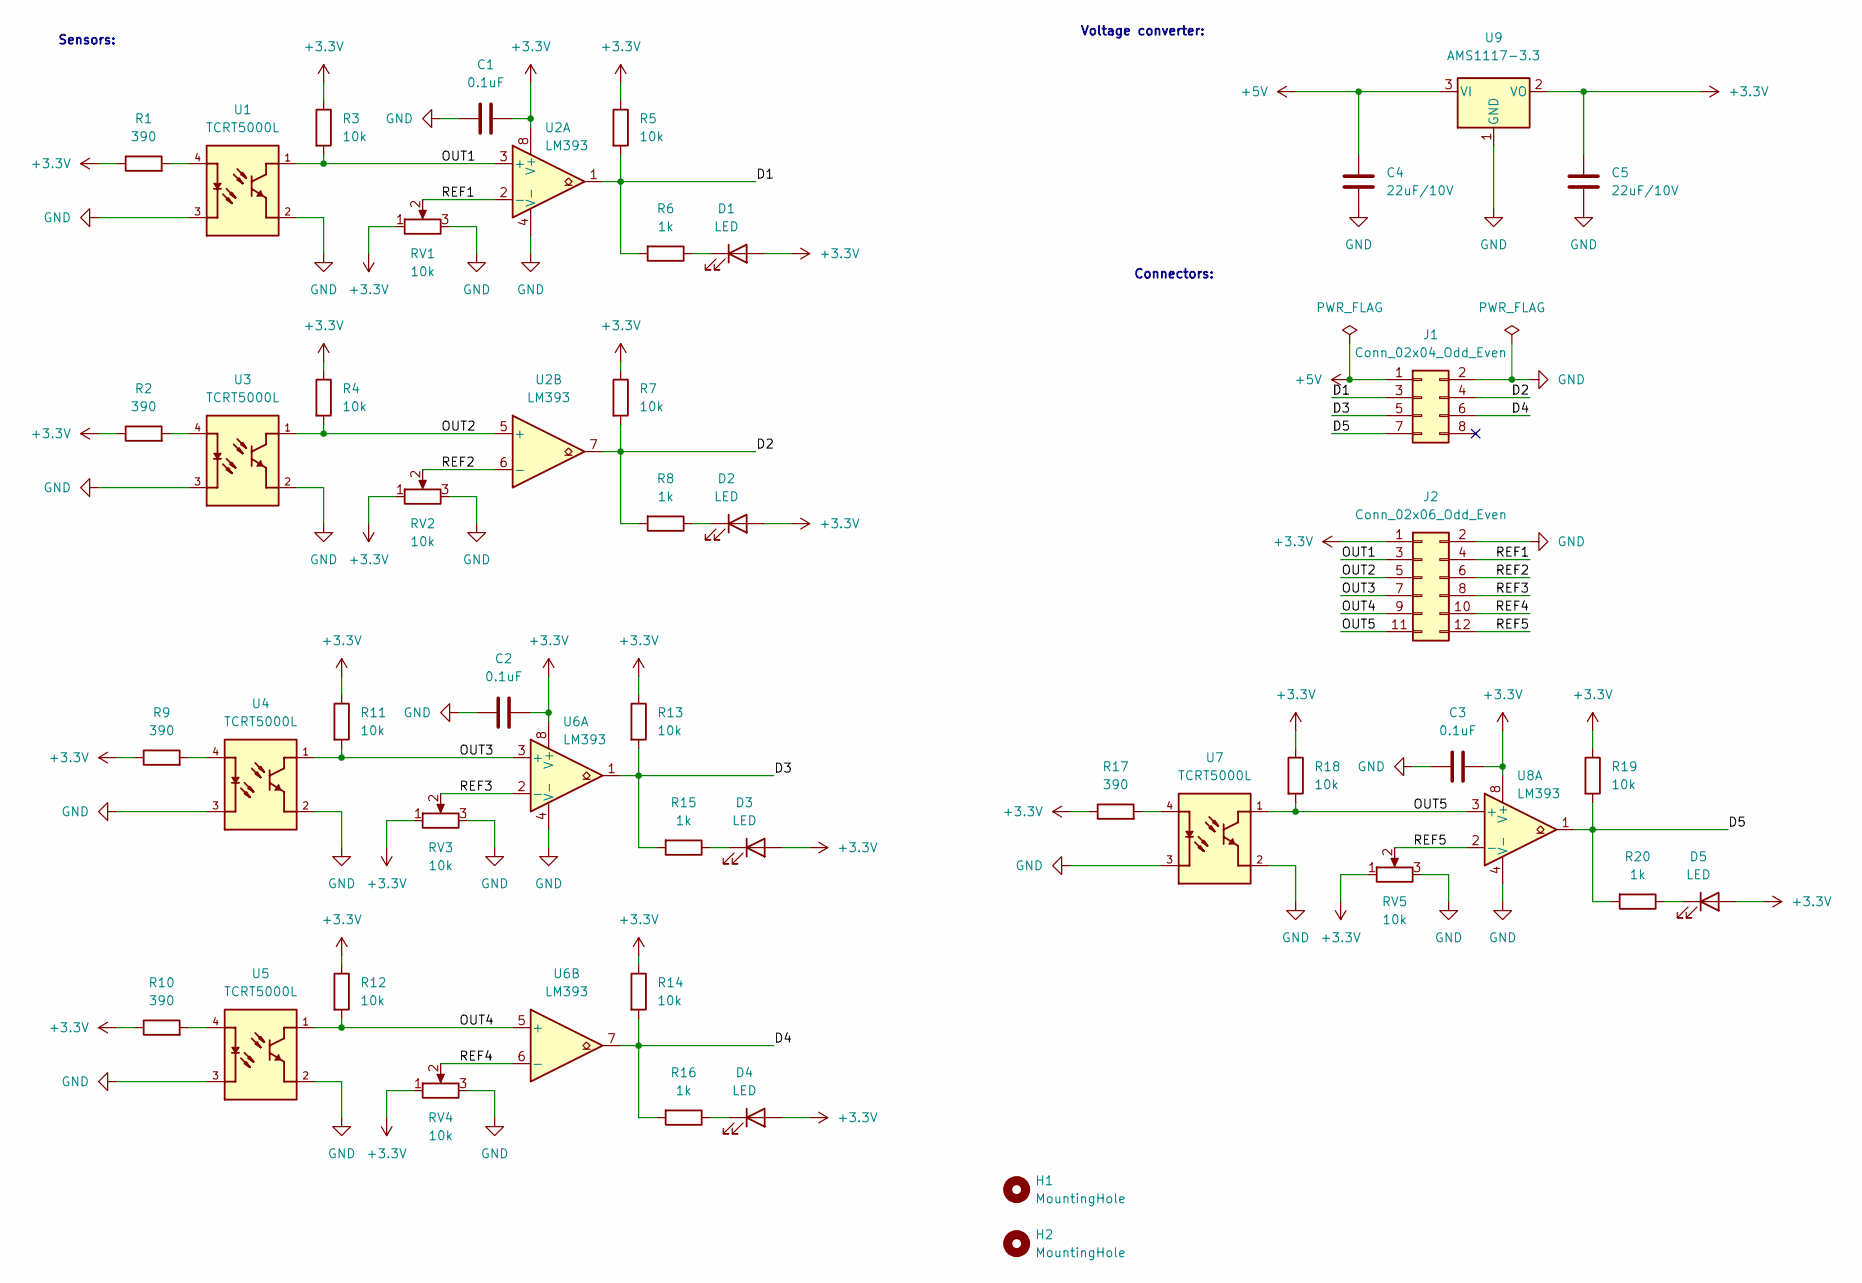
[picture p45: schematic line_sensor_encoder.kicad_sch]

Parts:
C1, C2, C3: 0.1uF; C_0805_2012Metric_Pad1.18x1.45mm_HandSolder
C4, C5: 22uF/10V; C_0805_2012Metric_Pad1.18x1.45mm_HandSolder
D1, D2, D3, D4, D5: LED; LED_0805_2012Metric_Pad1.15x1.40mm_HandSolder
H1, H2: MountingHole; MountingHole_3.2mm_M3_DIN965
J1: Conn_02x04_Odd_Even; PinHeader_2x04_P2.54mm_Vertical
J2: Conn_02x06_Odd_Even; PinHeader_2x06_P2.54mm_Vertical
R1, R2, R9, R10, R17: 390; R_0805_2012Metric_Pad1.20x1.40mm_HandSolder
R3, R4, R5, R7, R11, R12, R13, R14, R18, R19: 10k; R_0805_2012Metric_Pad1.20x1.40mm_HandSolder
R6, R8, R15, R16, R20: 1k; R_0805_2012Metric_Pad1.20x1.40mm_HandSolder
RV1, RV2, RV3, RV4, RV5: 10k; Potentiometer_Bourns_3296W_Vertical
U1, U3, U4, U5, U7: TCRT5000L; XDCR_TCRT5000L
U2, U6, U8: LM393; SOP-8_5.28x5.23mm_P1.27mm
U9: AMS1117-3.3; SOT-223-3_TabPin2

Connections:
+3.3V: C1.2, C2.2, C3.2, C5.1, D1.2 (A), D2.2 (A), D3.2 (A), D4.2 (A), D5.2 (A), J2.1, R1.1, R2.1, R3.1, R4.1, R5.1, R7.1, R9.1, R10.1, R11.1, R12.1, R13.1, R14.1, R17.1, R18.1, R19.1, RV1.1, RV2.1, RV3.1, RV4.1, RV5.1, U2.8 (V+), U6.8 (V+), U8.8 (V+), U9.2 (VO)
+5V: C4.1, J1.1, U9.3 (VI)
/D1: J1.3, R5.2, R6.2, U2.1
/D2: J1.4, R7.2, R8.2, U2.7
/D3: J1.5, R13.2, R15.2, U6.1
/D4: J1.6, R14.2, R16.2, U6.7
/D5: J1.7, R19.2, R20.2, U8.1
/OUT1: J2.3, R3.2, U1.1, U2.3 (+)
/OUT2: J2.5, R4.2, U2.5 (+), U3.1
/OUT3: J2.7, R11.2, U4.1, U6.3 (+)
/OUT4: J2.9, R12.2, U5.1, U6.5 (+)
/OUT5: J2.11, R18.2, U7.1, U8.3 (+)
/REF1: J2.4, RV1.2, U2.2 (-)
/REF2: J2.6, RV2.2, U2.6 (-)
/REF3: J2.8, RV3.2, U6.2 (-)
/REF4: J2.10, RV4.2, U6.6 (-)
/REF5: J2.12, RV5.2, U8.2 (-)
GND: C1.1, C2.1, C3.1, C4.2, C5.2, J1.2, J2.2, RV1.3, RV2.3, RV3.3, RV4.3, RV5.3, U1.2, U1.3, U2.4 (V-), U3.2, U3.3, U4.2, U4.3, U5.2, U5.3, U6.4 (V-), U7.2, U7.3, U8.4 (V-), U9.1 (GND)
unnamed: D1.1 (K), R6.1
unnamed: D2.1 (K), R8.1
unnamed: D3.1 (K), R15.1
unnamed: D4.1 (K), R16.1
unnamed: D5.1 (K), R20.1
unnamed: R1.2, U1.4
unnamed: R2.2, U3.4
unnamed: R9.2, U4.4
unnamed: R10.2, U5.4
unnamed: R17.2, U7.4

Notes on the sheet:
Sensors:
Connectors:
Voltage converter:

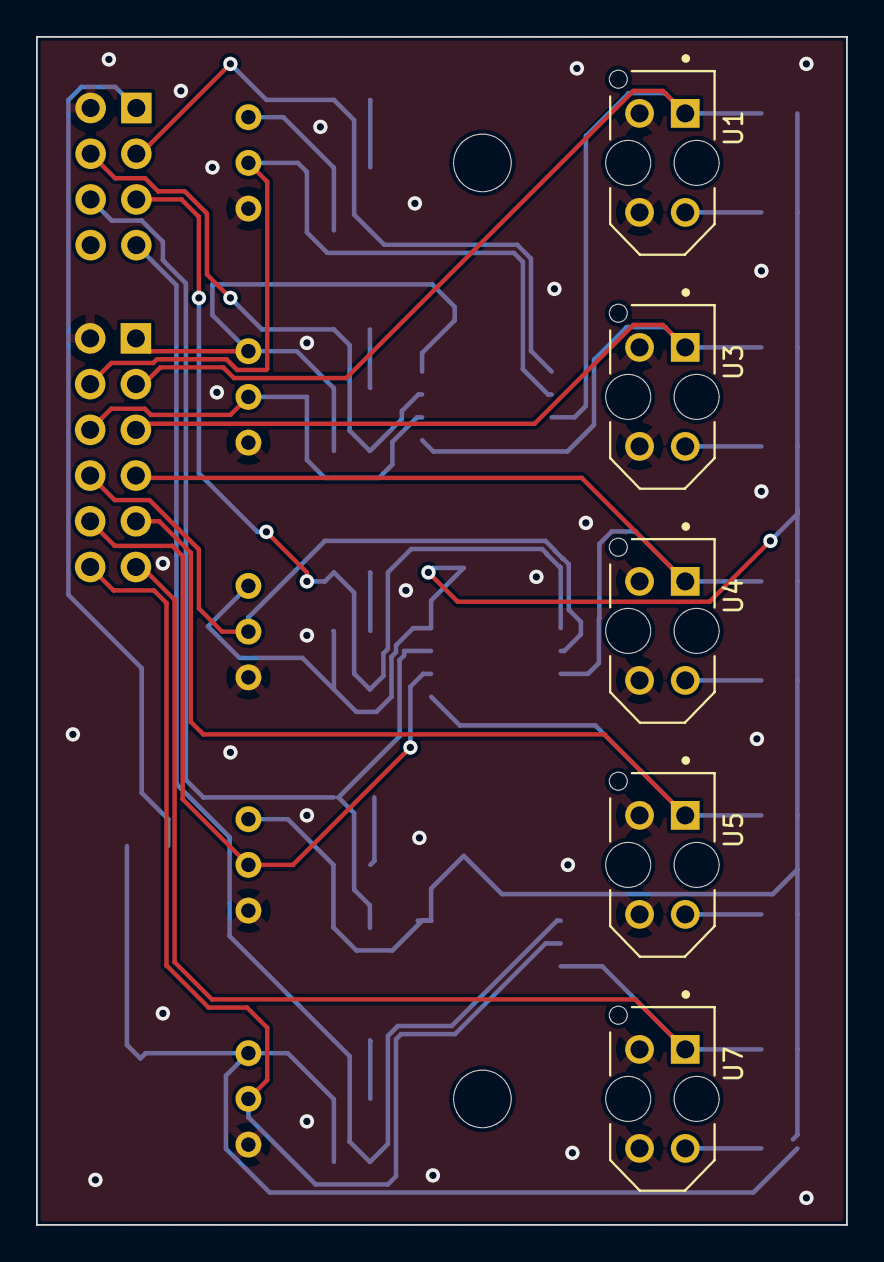
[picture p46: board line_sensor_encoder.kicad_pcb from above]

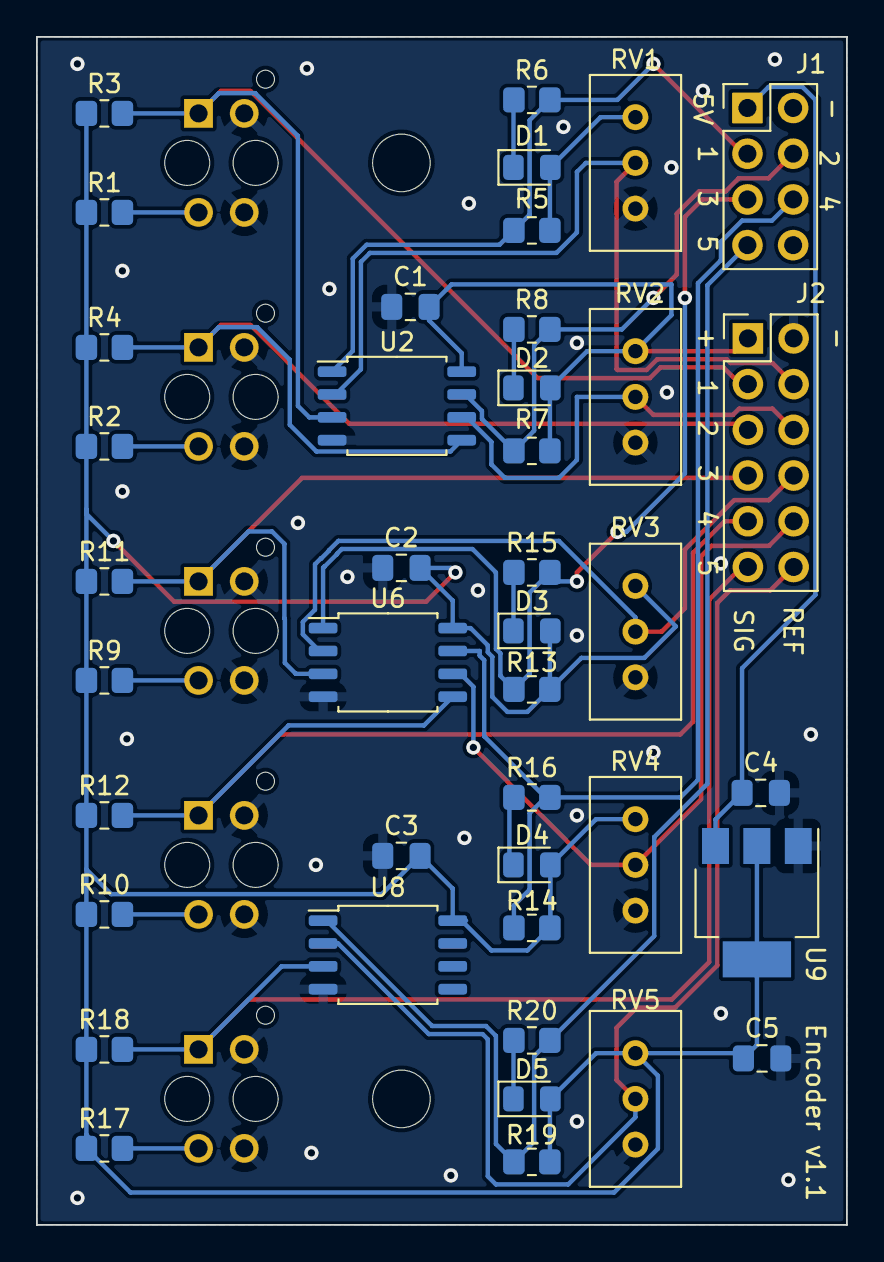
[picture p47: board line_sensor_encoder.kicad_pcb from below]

Board: 2 copper layers, 45.0 x 66.0 mm, 48 parts (43 on the bottom side), 28 nets.

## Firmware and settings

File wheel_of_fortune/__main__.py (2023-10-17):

import os
import logging
import coloredlogs
import importlib.metadata
from .dependencies import startup_event, shutdown_event
from .routers import encoder
from .routers import servos
from .routers import leds
from .routers import soundsystem
from .routers import wheel
from .routers import ws

import uvicorn
from fastapi import FastAPI
from fastapi.middleware.cors import CORSMiddleware
from fastapi.staticfiles import StaticFiles

_LOGGER = logging.getLogger(__name__)
_VERSION = importlib.metadata.version("wheel_of_fortune")

coloredlogs.install(
    level="debug",
    fmt="%(asctime)s %(name)s:%(lineno)d %(levelname)s %(message)s",
    milliseconds=True,
)

app = FastAPI(docs_url="/api/v1/docs", openapi_url="/api/v1/openapi.json")

app.include_router(encoder.router)
app.include_router(servos.router)
app.include_router(leds.router)
app.include_router(soundsystem.router)
app.include_router(wheel.router)
app.include_router(ws.router)

app.add_middleware(
    CORSMiddleware,
    allow_origins=["*"],
    allow_credentials=True,
    allow_methods=["*"],
    allow_headers=["*"],
)

local_www_path = os.environ.get("LOCAL_WWW_PATH")
if local_www_path is not None:
    if os.path.isdir(local_www_path):
        _LOGGER.info("local www path: %s" % (local_www_path))
        app.mount(
            "/local", StaticFiles(directory=local_www_path, html=True), name="local"
        )
    else:
        _LOGGER.warning("local www path does not exist: %s" % (local_www_path))

frontend_path = os.path.join(os.path.dirname(__file__), "frontend", "dist")
if os.path.isdir(frontend_path):
    app.mount("/", StaticFiles(directory=frontend_path, html=True), name="frontend")
else:
    _LOGGER.warning("frontend path does not exist: %s" % (frontend_path))


@app.on_event("startup")
async def api_startup_event():
    _LOGGER.info("version: %s" % (_VERSION))
    _LOGGER.info("startup_event")
    await startup_event()


@app.on_event("shutdown")
async def api_shutdown_event():
    _LOGGER.info("shutdown_event")
    await shutdown_event()


if __name__ == "__main__":
    uvicorn.run(app, host="0.0.0.0", port=8000)

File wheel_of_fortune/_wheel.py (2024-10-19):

import os
import asyncio
import logging
import importlib.metadata
from enum import Enum
from typing import Callable
from ._utils import gather_or_cancel
from ._config import Config
from ._settings import SettingsManager, Settings
from ._encoder import Encoder
from ._leds import LedController
from ._servos import ServoController
from ._soundsystem import SoundSystem, MAIN_CH, EFFECT_CH
from ._telemetry import Telemetry, Point
from ._themes import load_themes, Theme
from ._effects import load_effects, Effect
from .schemas import (
    EncoderState,
    LedsState,
    LedsStateIn,
    ServosState,
    SoundSystemState,
    SectorState,
    SectorStateIn,
    WheelState,
    WheelStateIn,
    WheelInfo,
    WheelStateUpdate,
)

_LOGGER = logging.getLogger(__name__)
VERSION = importlib.metadata.version("wheel_of_fortune")

__all__ = [
    "Wheel",
]


class TaskType(Enum):
    STARTUP = "startup"
    IDLE = "idle"
    SPINNING = "spinning"
    STOPPED = "stopped"
    STANDBY = "standby"
    POWEROFF = "poweroff"
    UNKNOWN = "unknown"


class Sector:
    def __init__(self, index, settings, effects):
        self.index: int = index
        self._settings: Settings = settings
        self._effects: dict[str, Effect] = effects
        self.name: str = "sector %d" % (index)
        self.effect_id: str = list(effects.keys())[0]

    def init(self):
        if "name" in self._settings:
            self.name = self._settings["name"]
        if "effect_id" in self._settings:
            self.effect_id = self._settings["effect_id"]

    def set_state(self, state: SectorStateIn):
        _LOGGER.info("set state %d: %s" % (self.index, state))
        if state.name is not None:
            self.name = state.name
            self._settings.set("name", self.name)
        if state.effect_id is not None:
            if state.effect_id not in self._effects:
                raise ValueError("unknown effect id")
            self.effect_id = state.effect_id
            self._settings.set("effect_id", self.effect_id)

    def get_state(self) -> SectorState:
        return SectorState(
            index=self.index,
            name=self.name,
            effect_id=self.effect_id,
        )

    @property
    def effect(self) -> Effect:
        return self._effects[self.effect_id]


class Wheel:
    def __init__(self, config, gpio):
        self._config: Config = config
        self._loop = asyncio.get_running_loop()
        self._gpio = gpio
        self._subscriptions: list[Callable[[WheelStateUpdate], None]] = []

        self._poweroff_pin = "PL8"
        self._gpio.setup(
            self._poweroff_pin, self._gpio.IN, pull_up_down=self._gpio.PUD_OFF
        )

        settings_file = os.path.join(self._config.data_dir, "settings.json")
        self._settings_mgr = SettingsManager(settings_file)
        self._settings = self._settings_mgr["wheel"]

        self._telemetry = Telemetry(config)
        self._encoder = Encoder(
            config, self._gpio, self._telemetry, self._encoder_update
        )
        self._leds = LedController(
            config, self._settings_mgr["leds"], self._leds_update
        )
        self._servos = ServoController(config, self._servos_update)
        self._soundsystem = SoundSystem(
            config, self._settings_mgr["sound"], self._soundsystem_update
        )

        self._active_task: asyncio.Task | None = None
        self._cancelling_active_task: bool = False
        self._next_task: TaskType = TaskType.STARTUP

        themes_file = os.path.join(config.data_dir, "themes.yaml")
        self._themes = load_themes(themes_file)
        self._theme_id: str = list(self._themes.keys())[0]
        self._standby_timer: float = 600

        effects_file = os.path.join(config.data_dir, "effects.yaml")
        self._effects = load_effects(effects_file)

        self._sectors: list[Sector] = []
        for i in range(config.num_sectors):
            sector_settings = self._settings.subsettings("sectors").subsettings(
                "%d" % (i)
            )
            self._sectors.append(Sector(i, sector_settings, self._effects))

    async def init(self):
        _LOGGER.info("init")

        # Open settings
        await self._settings_mgr.open()
        if "theme_id" in self._settings:
            theme_id = self._settings["theme_id"]
            if theme_id in self._themes:
                self._theme_id = theme_id
            else:
                _LOGGER.warning("unknown theme id: %s" % (theme_id))

        if "standby_timer" in self._settings:
            self._standby_timer = self._settings["standby_timer"]

        for sector in self._sectors:
            sector.init()

        # Open connections
        await asyncio.gather(
            self._telemetry.open(),
            self._encoder.open(),
            self._leds.open(),
            self._servos.open(),
            self._soundsystem.open(),
        )

    async def close(self):
        _LOGGER.info("close")
        await asyncio.gather(
            self._settings_mgr.close(),
            self._telemetry.close(),
            self._leds.close(),
            self._servos.close(),
            self._encoder.close(),
            self._soundsystem.close(),
        )
        if self._active_task is not None and not self._active_task.done():
            self._active_task.cancel()

    async def set_state(self, state: WheelStateIn):
        if state.active_task is not None:
            _LOGGER.info("activate task: %s" % (state.active_task))
            self._schedule_task(TaskType(state.active_task))

        if state.theme_id is not None:
            _LOGGER.info("activate theme: %s" % (state.theme_id))
            if state.theme_id in self._themes:
                self._theme_id = state.theme_id
            else:
                raise ValueError("unknown theme name")
            self._settings.set("theme_id", self._theme_id)
            self._publish_update(
                WheelStateUpdate(
                    theme_id=self._theme_id,
                )
            )

        if state.standby_timer is not None:
            _LOGGER.info("set stadby timer: %s" % (state.standby_timer))
            self._standby_timer = state.standby_timer
            self._settings.set("standby_timer", self._standby_timer)
            self._publish_update(
                WheelStateUpdate(
                    standby_timer=self._standby_timer,
                )
            )

        if len(state.sectors) > 0:
            for index, sector_state in state.sectors.items():
                if index < 0 or index >= len(self._sectors):
                    raise ValueError("Sector index out of bounds")
                sector = self._sectors[index]
                sector.set_state(sector_state)

            self._publish_update(
                WheelStateUpdate(
                    sectors=[sector.get_state() for sector in self._sectors]
                )
            )
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

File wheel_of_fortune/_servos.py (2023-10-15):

import asyncio
import aiohttp
import logging
from typing import Callable
from ._config import Config
from .schemas import (
    ServoState,
    ServoStateIn,
    ServoInfo,
    ServosState,
    ServosStateIn,
    ServosInfo,
)

_LOGGER = logging.getLogger(__name__)


class ServoMotor:
    def __init__(self, pwm_id, mount_angle, zero_duty, full_duty, mount_duty):
        self.pwm_id = pwm_id
        self._mount_angle = mount_angle
        self._zero_duty = zero_duty
        self._full_duty = full_duty
        self._mount_duty = mount_duty

        self._pos = 0.0
        self._detached = True

    def set_state(self, state: ServoStateIn):
        if state.pos is not None:
            self._pos = state.pos
        if state.detached is not None:
            self._detached = state.detached

    def get_state(self) -> ServoState:
        return ServoState(
            pos=self._pos,
            duty=self.get_duty(),
            detached=self._detached,
        )

    def get_info(self) -> ServoInfo:
        return ServoInfo(
            mount_angle=self._mount_angle,
            zero_duty=self._zero_duty,
            full_duty=self._full_duty,
            mount_duty=self._mount_duty,
            mount_pos=self._duty_to_pos(self._mount_duty) or 1.0,
        )

    def get_duty(self):
        if self._detached:
            return 0.0
        return self._pos_to_duty(self._pos)

    def _pos_to_duty(self, pos: float | None) -> float:
        if pos is None:
            return 0.0
        return pos * (self._full_duty - self._zero_duty) + self._zero_duty

    def _duty_to_pos(self, duty: float) -> float | None:
        if duty == 0.0:
            return None
        return (duty - self._zero_duty) / (self._full_duty - self._zero_duty)


class ServoController:
    def __init__(self, config, update_cb):
        self._config: Config = config
        self._update_cb: Callable[[ServosState], None] = update_cb
        self._loop = asyncio.get_running_loop()
        self._session: aiohttp.ClientSession | None = None
        self._info = {}

        self._motors = {}
        for i, servo_conf in enumerate(config.servos):
            pwm_id = "%d" % (i)
            self._motors[servo_conf.name] = ServoMotor(
                pwm_id,
                servo_conf.mount_angle,
                self._config.servo_zero_duty,
                self._config.servo_full_duty,
                self._config.servo_mount_duty,
            )

    async def open(self):
        _LOGGER.info("open")
        self._session = aiohttp.ClientSession(
            base_url=self._config.wled_url,  # type: ignore
            raise_for_status=True,  # type: ignore
        )
        resp = await self._session.get("/json/info")
        self._info = await resp.json()
        _LOGGER.debug("info: %s" % (self._info))

    async def close(self):
        if self._session is None:
            return
        _LOGGER.info("close")
        await self._session.close()
        _LOGGER.info("close done.")

    async def set_state(self, state: ServosStateIn):
        _LOGGER.info("set_state: %s" % (state))
        for name, motor in self._motors.items():
            if name in state.motors:
                motor.set_state(state.motors[name])
        await self._sync_state()

    def get_state(self) -> ServosState:
        return ServosState(
            motors={name: motor.get_state() for name, motor in self._motors.items()}
        )

    def get_info(self) -> ServosInfo:
        return ServosInfo(
            version=self._info.get("ver", ""),
            motors={name: motor.get_info() for name, motor in self._motors.items()},
        )

    async def maintain(self):
        while True:
            # state = self.get_state()
            # _LOGGER.info("servos state: %s" % (state))
            await asyncio.sleep(100.0)

    async def move_to_pos(
        self, target_pos: float, motor_names: list[str] | None = None
    ):
        _LOGGER.info(
            "move to pos: motors: %s, target: %.3f" % (motor_names, target_pos)
        )

        if motor_names is None:
            selected_motors = self._motors
        else:
            selected_motors = {}
            for name in motor_names:
                if name not in self._motors:
                    _LOGGER.warning("unknown servo name: %s" % (name))
                    continue
                selected_motors[name] = self._motors[name]

        for name, motor in selected_motors.items():
            motor.set_state(ServoStateIn(pos=target_pos, detached=False))
        await self._sync_state()

    async def _sync_state(self):
        _LOGGER.info("sync state")
        if self._session is None:
            raise ConnectionError("Session is not opened")

        pwm_data = {}
        for motor in self._motors.values():
            pwm_data[motor.pwm_id] = {"duty": motor.get_duty()}

        await self._session.post("/json/state", json={"pwm": pwm_data})
        self._loop.call_soon(self._update_cb, self.get_state())

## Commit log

2023-08-20 encoder code cleanup
2023-08-20 leds code cleanup
2023-08-21 only build wheel
2023-08-21 pin version
2023-08-23 added description for wheel-of-fortune telemetry
2023-08-24 Squashed 'embedded_software/WLED/' content from commit 04aa9f0e
    git-subtree-dir: embedded_software/WLED
    git-subtree-split: 04aa9f0e617c152894087aaec843f9060b1c86a2
    [IR_Remote_Codes.xlsx, WLED_ESP32-wrover_4MB.csv, WLED_ESP32_16MB.csv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]
2023-08-24 enabled PWM usermod
2023-08-25 Added readme to gpio-poweroff service
2023-08-26 use EncoderState schema in encoder
2023-08-26 use schemas in led controller
2023-08-26 use schemas in servos controller
2023-08-26 use schemas in wheel
2023-08-27 full wheel state
2023-08-27 updated encoder callback
2023-08-27 added update callback to led controller
2023-08-27 reworked servo controller
2023-08-28 small code style fix
    [_wheel.py]
2023-08-29 implemented throttled slider
2023-08-29 disable threads to save memory
2023-08-30 reorganized wheel svg
2023-08-30 rudimentary support for servos
2023-08-30 use servo state
2023-08-30 added servos info
2023-08-30 use servo info
2023-08-31 remove esp32c3dev
2023-08-31 added startup and poweroff sounds
2023-08-31 better ws error handling
    [_ws_manager.py]
2023-08-31 fix wheel position
2023-08-31 added possibility to activate servos per effect
2023-09-02 added pinout sheet
    [olimex esp32 pinout.xlsx]
2023-09-02 added wiring diagram
2023-09-02 encoder pattern
2023-09-02 line encoder
    [C_0805_2012Metric.step, LED_0805_2012Metric.step, PinHeader_2x04_P2.54mm_Vertical.step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]
2023-09-02 added 3.3V dc converter
    [SOT-223.step, TCRT5000.step, TCRT5000L.step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]
2023-09-02 added title block
    [line_sensor_encoder.kicad_sch]
2023-09-02 updated wiring diagram
2023-09-02 added drawings for amplifier
    [amplifer cover.STL, amplifer mount.STL]
2023-09-02 amplifier assembly
2023-09-02 helper script to rotate STL files
2023-09-02 rotated STL files
    [amplifer cover.STL, amplifer mount.STL]
2023-09-02 compute models
    [compute cover.STL, compute mount.STL]
2023-09-02 correct folder
    [compute cover.STL, compute mount.STL]
2023-09-02 fix orientation
    [compute mount.STL]
2023-09-02 added dc converter models
    [dc converter assembly.STL, dc converter cover.STL, dc converter mount.STL]
2023-09-02 added encoder
    [encoder assembly.STL, encoder mount.STL]
2023-09-02 added limit wheel assembly
    [limit wheel assembly.STL, limit wheel mount.STL]
2023-09-02 mains relay assembly
    [mains relay assembly.STL, relay cover.STL, relay mount.STL]
2023-09-02 power switch assembly
    [power switch assembly.STL, switch mount.STL]
2023-09-02 linear actuator
    [demo logo.STL, gear rack.STL, gear.STL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]
2023-09-02 cover subassembly
    [cover assembly.STL, cover base.STL, cover led ring.STL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]
2023-09-02 wheel subassembly
    [bearing hub ext.STL, drill aid 2.STL, drill aid.STL]
2023-09-02 added flipper subassembly
    [flipper bumper.STL, flipper damper.STL, flipper fixed spring cover.STL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]
2023-09-02 speaker subassembly
    [speaker, stud1.STL, speaker, stud2.STL, speaker.STL]
2023-09-03 fix servo config
2023-09-03 tun servo speed
2023-09-08 fixes for servo motors
    [_servos.py, _wheel.py]
2023-09-08 fix for fast theme song fadeout
    [_wheel.py]
2023-09-09 removed ping causing fatal error if connection to influxdb fails
    [_telemetry.py]
2023-09-10 added more 3D models
    [demo logo.STL, encoder assembly.STL, encoder mount.STL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]
2023-09-10 added backplate assembly
2023-09-10 document 3D printer settings
2023-09-15 added image for backlight leds
2023-09-17 added drawings for backplate and wheel
2023-09-17 added bom
    [bom.xlsx]
2023-09-18 added info about limit wheels
2023-09-18 rename files
    [power relay assembly.STL, relay cover.STL, relay mount.STL]
2023-09-18 moved bom to separate directory
    [bom.xlsx]
2023-09-18 fix wrong directory
    [bom.xlsx]
2023-10-11 updated default servo pos
2023-10-13 catch all telemetry reporting errors
    [_telemetry.py]
2023-10-13 cancel all maintain tasks if one fails/is cancelled
    [_utils.py, _wheel.py]
2023-10-13 report servo mount pos
2023-10-15 add default led transition value
2023-10-17 support led transitions
2023-10-17 add leds transition
2023-10-17 larger slider buttons
2023-10-17 reworked servo page
2023-10-17 test different mount order
2023-10-18 fix default logo location
    [_config.py]
2023-12-20 Update ghcr.io/ardiloot/wheel-of-fortune Docker tag to v1.1.0
2024-10-10 do not allow effect to be interrupted
2024-10-19 allow high speeds spins interrupt playing effect
2024-10-20 Update ghcr.io/ardiloot/wheel-of-fortune Docker tag to v1.2.0

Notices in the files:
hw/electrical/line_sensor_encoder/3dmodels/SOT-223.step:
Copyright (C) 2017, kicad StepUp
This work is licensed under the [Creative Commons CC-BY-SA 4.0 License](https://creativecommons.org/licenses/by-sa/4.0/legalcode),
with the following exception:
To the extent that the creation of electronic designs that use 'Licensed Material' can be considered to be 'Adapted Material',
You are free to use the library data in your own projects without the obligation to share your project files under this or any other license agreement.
